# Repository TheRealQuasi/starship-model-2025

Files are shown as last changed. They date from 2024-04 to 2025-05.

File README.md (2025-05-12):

# Starship model Project 2025

Modelling and control of an electric reusable rocket
----------------------------------------------------

This project is part of a bachelor theisis at Chalmers University of Technology, department of electrical engineering ([Full report](/Bachelor_thesis_EENX16_24_50_Starship.pdf)
).

It is a continuation of a previous bachlor thesis from 2023, with the goal of buidling a propeller driven rocket model, immitating the control of SpaceX starships second stage.

The project involves programming a Teensy 4.1 microcontroller using PlatformIO in Visual Studio Code.

## Setup

1. Install Visual Studio Code.
2. Install the PlatformIO extension in Visual Studio Code.
3. Open the `Starship_25` folder in Visual Studio Code. PlatformIO should automatically detect all necessary files.

## Building and Programming

1. Connect the Teensy 4.1 microcontroller to your PC via USB.
2. Build the project by clicking on the checkmark icon in the bottom left corner of the PlatformIO interface.
3. Program the microcontroller by clicking on the arrow icon next to the checkmark.

## Dependencies

This project depends on the following libraries:

https://github.com/Seeed-Studio/Grove_6Axis_Accelerometer_And_Gyroscope_BMI088.git
https://github.com/budryerson/TFMini-Plus-I2C
https://github.com/bitcraze/Bitcraze_PMW3901

Please ensure these libraries are installed with platformIO before building the project. They should however be installed automatically when opening the project.

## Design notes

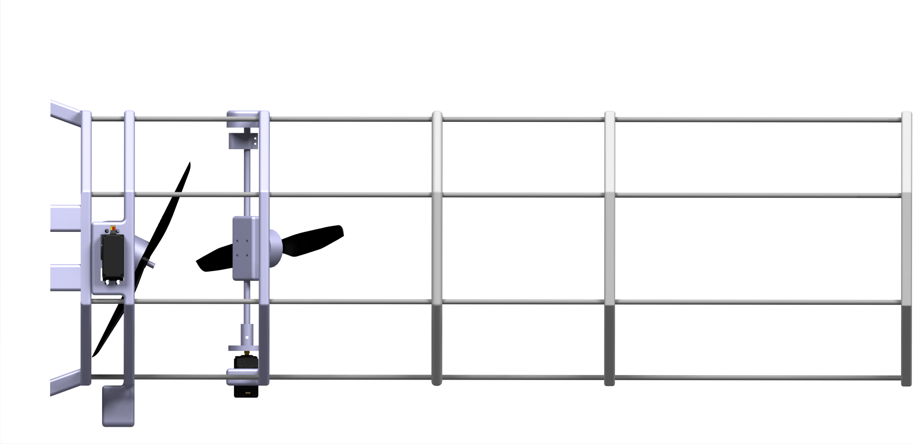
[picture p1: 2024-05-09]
CAD/Renders/Starship_render_sida1.png

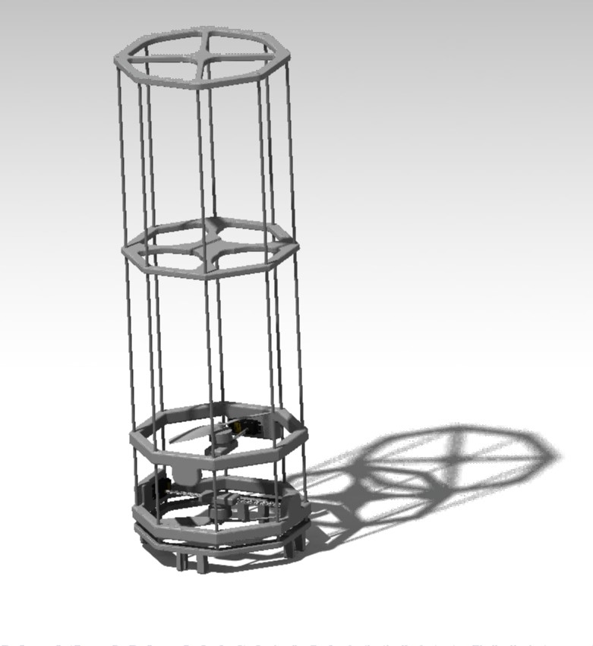
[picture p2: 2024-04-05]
CAD/Renders/Starship_render.jpg

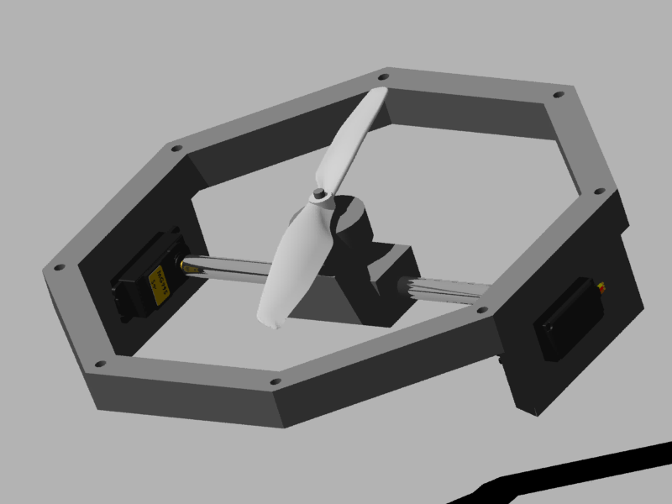
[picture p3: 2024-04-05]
CAD/Renders/Shooting 1.tif

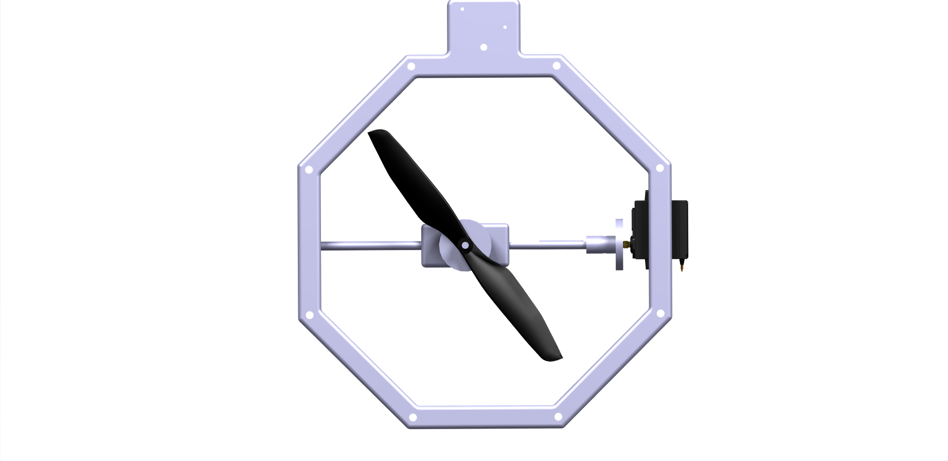
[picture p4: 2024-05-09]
CAD/Renders/Lidar_render.png

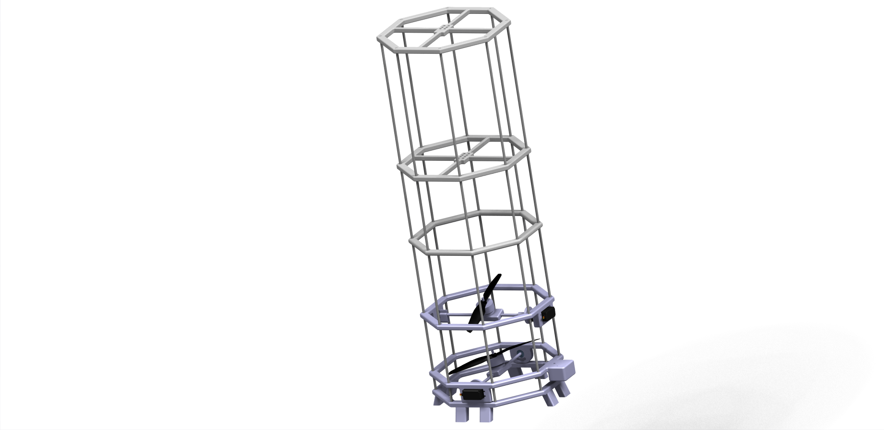
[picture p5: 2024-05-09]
CAD/Renders/Starship_render_startsida.png

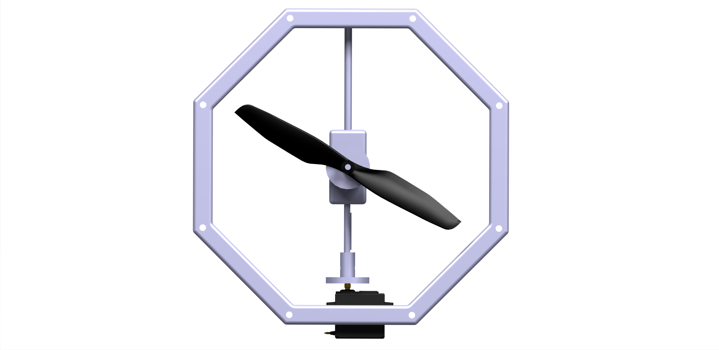
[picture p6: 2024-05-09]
CAD/Renders/Gimbal_render.png

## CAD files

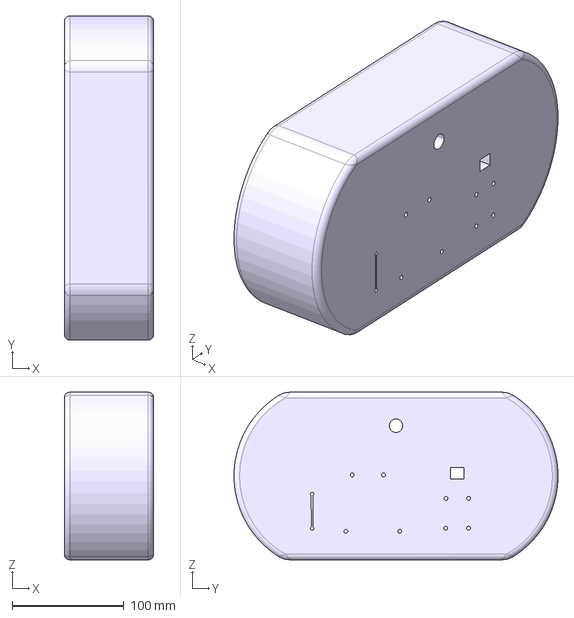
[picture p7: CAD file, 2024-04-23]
CAD/Prints/Handkontroll_Utskrift_1.stp
80.0 x 289.9 x 150.0 mm

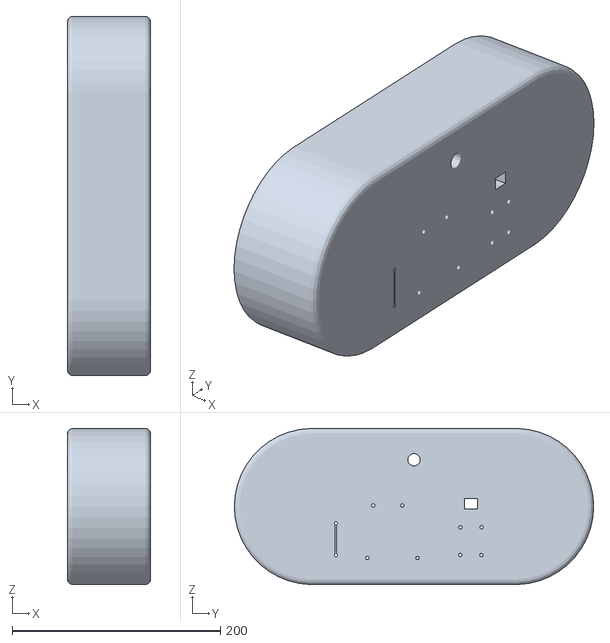
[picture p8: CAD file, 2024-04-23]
CAD/Prints/Handkontroll_utskrift_1.0.stl
80.0 x 345.5 x 150.0

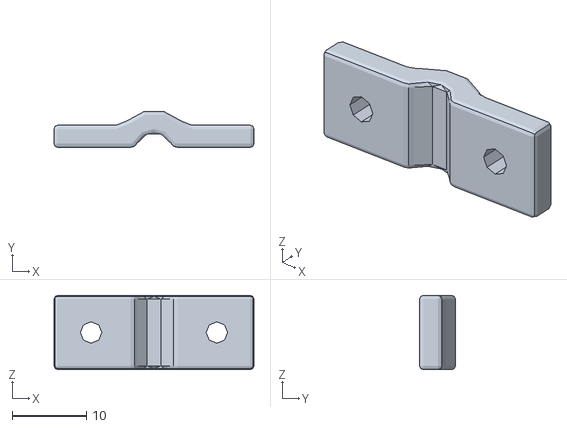
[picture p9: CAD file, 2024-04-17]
CAD/Prints/stav_klamma_utskrift.stl
27.0 x 4.83 x 10.0

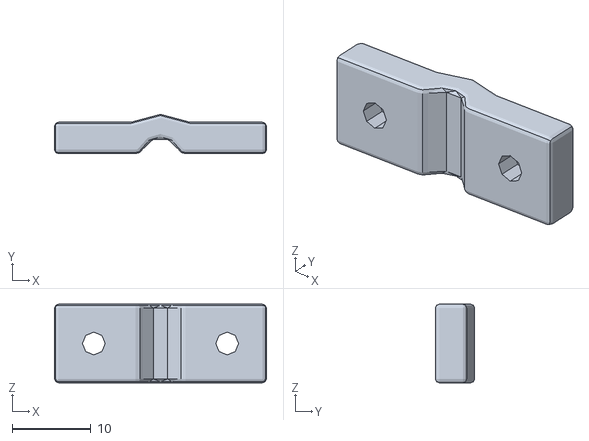
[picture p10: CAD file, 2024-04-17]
CAD/Prints/stav_mutterklamma_utskrift.stl
27.0 x 5.00 x 10.0

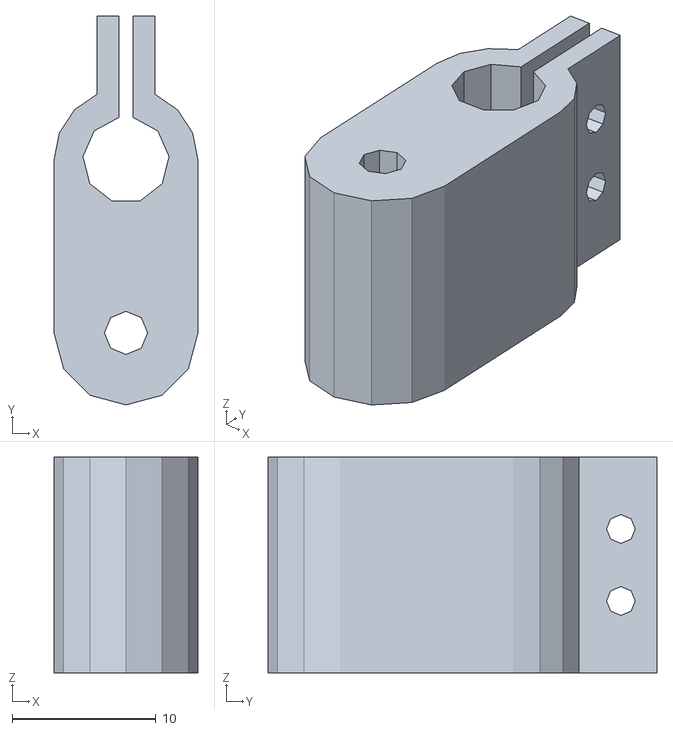
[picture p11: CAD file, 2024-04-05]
CAD/Prints/Klamma_stopp_utskrift_1.0.stl
10.0 x 27.0 x 15.0

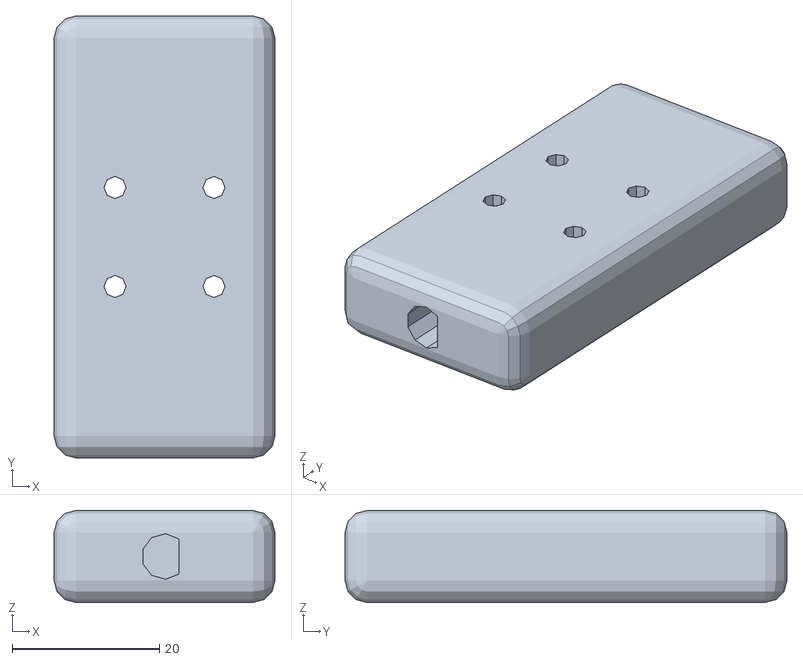
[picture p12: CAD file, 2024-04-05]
CAD/Prints/Blocktillmotorstang utskrift 1.1.stl
30.0 x 60.0 x 12.5

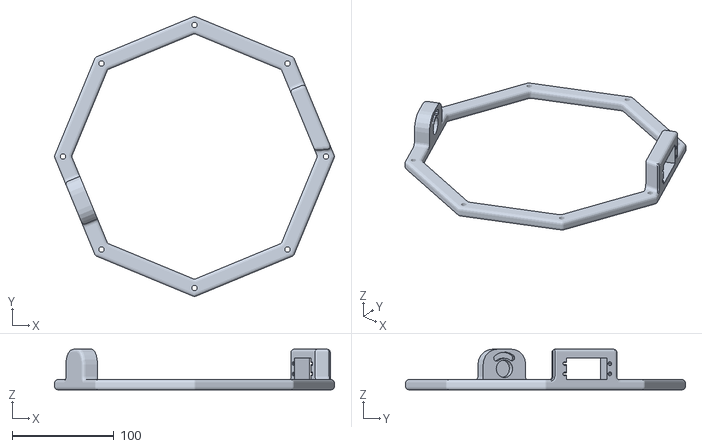
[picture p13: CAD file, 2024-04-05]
CAD/Prints/Hex_platta_utskrift_1.2.stl
275.5 x 275.5 x 40.0

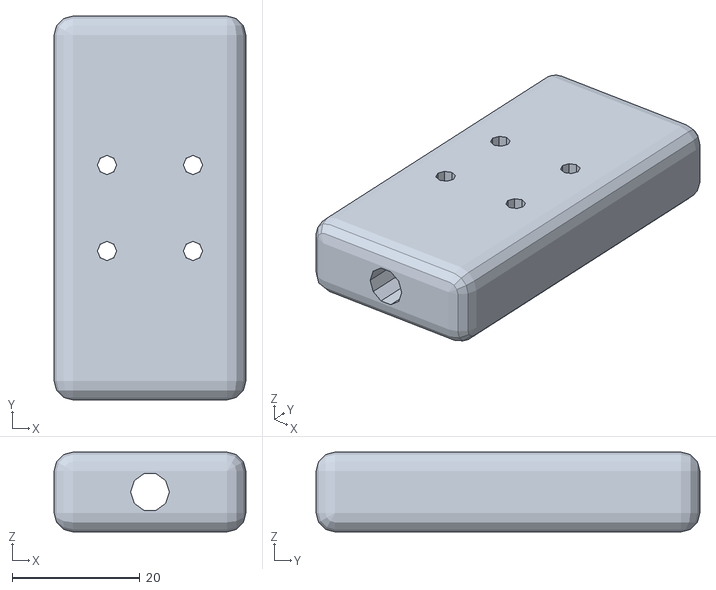
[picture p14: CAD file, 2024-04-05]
CAD/Prints/Blocktillmotorstang utskrift.stl
30.0 x 60.0 x 12.5

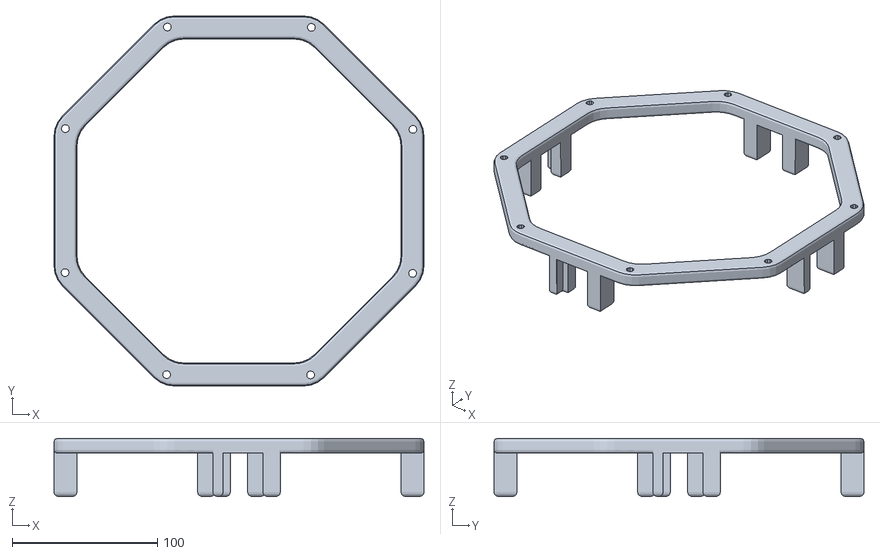
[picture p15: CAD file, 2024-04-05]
CAD/Prints/Bottenplatta_utskrift.stl
255.0 x 255.0 x 40.0

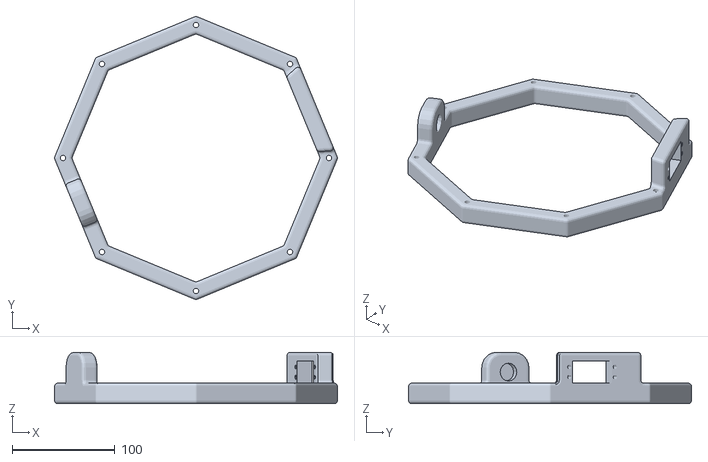
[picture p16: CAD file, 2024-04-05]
CAD/Prints/Hex_platta utskrift.stl
275.5 x 275.5 x 50.0

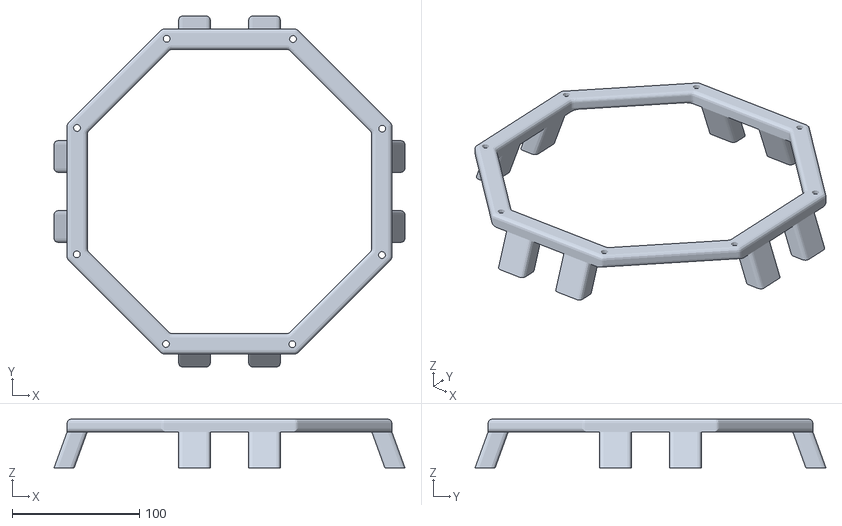
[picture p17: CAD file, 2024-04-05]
CAD/Prints/Bottenplatta_utskrift_1.stl
275.6 x 275.6 x 38.2

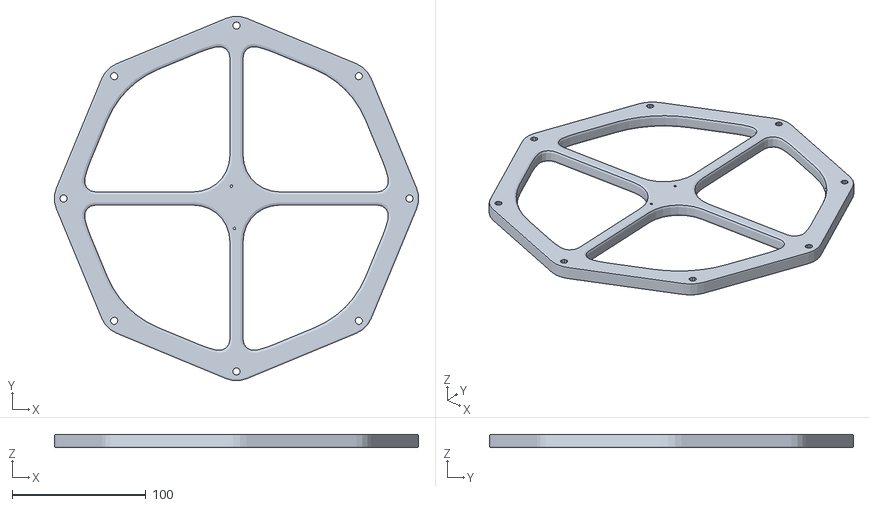
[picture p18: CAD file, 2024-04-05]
CAD/Prints/Toppplatta_utskrift.stl
272.4 x 272.4 x 10.0

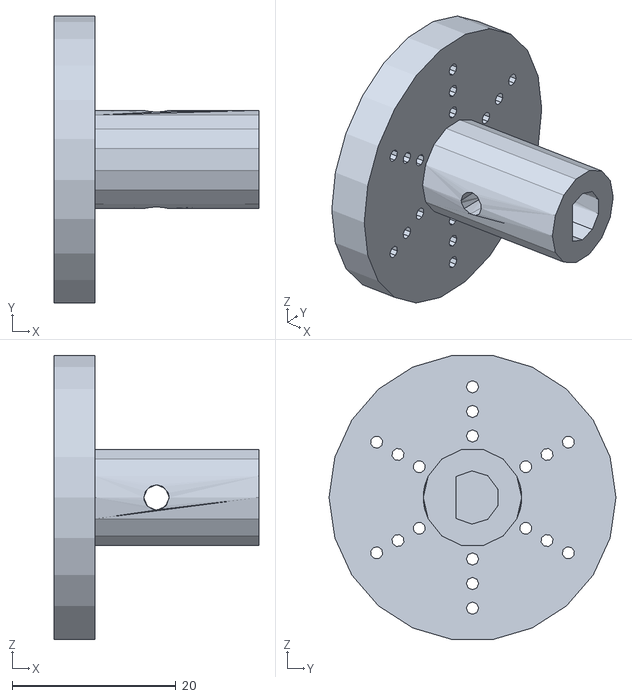
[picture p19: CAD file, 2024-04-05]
CAD/Prints/Klamma_stang_utskrift_1.1.stl
25.0 x 35.0 x 34.6

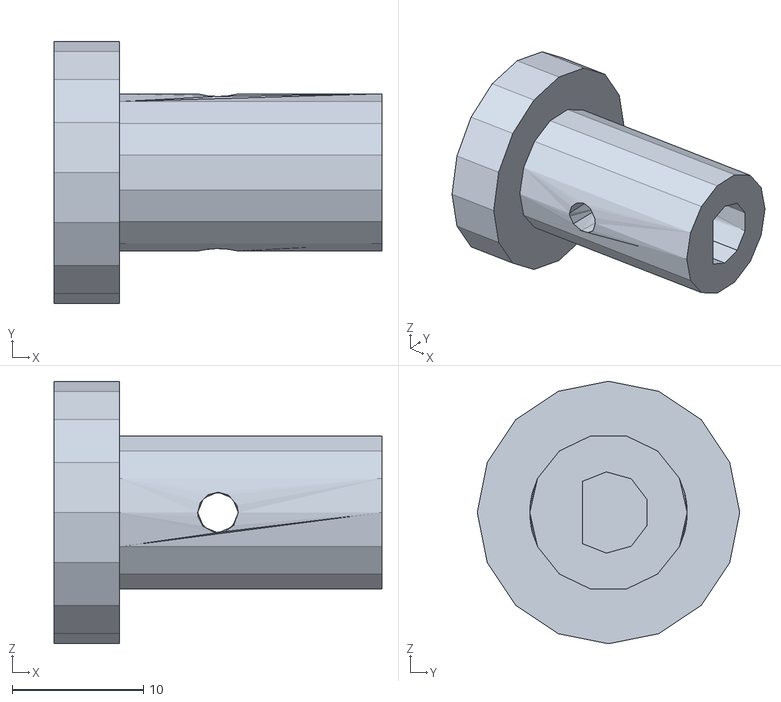
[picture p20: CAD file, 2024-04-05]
CAD/Prints/Klamma_stang_utskrift_1.0.stl
25.0 x 20.0 x 20.0

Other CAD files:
CAD/Prints/Hex_platta_utskrift_1.1.stl
CAD/Prints/Blocktillmotorstang_utskrift_1.2.stl
CAD/Prints/IMU_platta_utskrift_1.0.stl
CAD/Prints/TomPlatta_utskrift_1.0.stl
CAD/CAD_files/Blocktillmotorstang 1.0.CATPart
CAD/CAD_files/Blocktillmotorstang 1.1.CATPart
CAD/CAD_files/Bottenplatta.CATPart
CAD/CAD_files/Bottenplatta_1.1.CATPart
CAD/CAD_files/Handkontroll_1.0.CATPart
CAD/CAD_files/Handkontroll_1.1.CATPart
CAD/CAD_files/Hex_platta_1.0.CATPart
CAD/CAD_files/Hex_platta_1.1.CATPart
CAD/CAD_files/Hex_platta_1.2.CATPart
CAD/CAD_files/Hex_platta_1.3.CATPart
CAD/CAD_files/Hex_platta_1.4.CATPart
CAD/CAD_files/Klamma_stang_1.0.CATPart
CAD/CAD_files/Klamma_stang_1.1.CATPart
CAD/CAD_files/Klamma_stopp_1.0.CATPart
CAD/CAD_files/Kolfiberstang.CATPart
CAD/CAD_files/MG995.CATPart
CAD/CAD_files/Mittenplatta 1.0.CATPart
CAD/CAD_files/Mittenplatta 1.1.CATPart
CAD/CAD_files/Motorstang.CATPart
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

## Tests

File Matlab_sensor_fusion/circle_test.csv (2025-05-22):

timestamp | x1 | x2 | x3 | x4 | x5
2025-05-12T17:37:55.970376 | -0.01 | 0.02 | -6.77 | 3.05 | 0.01
2025-05-12T17:37:55.975332 | -0.01 | 0.02 | -6.77 | 3.05 | 0.01
2025-05-12T17:37:55.980794 | -0.01 | 0.02 | -6.77 | 3.05 | 0.02
2025-05-12T17:37:55.985734 | -0.01 | 0.02 | -6.77 | 3.05 | 0.01
2025-05-12T17:37:55.990682 | -0.01 | 0.02 | -6.77 | 3.05 | 0.01
2025-05-12T17:37:55.995787 | -0.01 | 0.02 | -6.77 | 3.05 | 0.01
2025-05-12T17:37:56.000909 | -0.01 | 0.02 | -6.77 | 3.05 | 0.01
2025-05-12T17:37:56.011162 | --0.01 | 0.02 | -6.77 | 3.05 | 0.01
2025-05-12T17:37:56.016248 | -0.01 | 0.02 | -6.77 | 3.05 | 0.02
2025-05-12T17:37:56.026483 | -0.0-0.01 | 0.02 | -6.77 | 3.05 | 0.01
2025-05-12T17:37:56.031572 | -0.01 | 0.02 | -6.77 | 3.05 | 0.02
2025-05-12T17:37:56.036802 | -0.01 | 0.02 | -6.77 | 3.05 | 0.02
2025-05-12T17:37:56.041821 | -0.01 | 0.02 | -6.77 | 3.05 | 0.01
2025-05-12T17:37:56.046927 | -0.01 | 0.02 | -6.77 | 3.05 | 0.01
2025-05-12T17:37:56.052062 | -0.01 | 0.02 | -6.77 | 3.05 | 0.02
2025-05-12T17:37:56.057142 | -0.01 | 0.02 | -6.77 | 3.05 | 0.01
2025-05-12T17:37:56.062260 | -0.01 | 0.02 | -6.77 | 3.05 | 0.01
2025-05-12T17:37:56.067464 | -0.01 | 0.02 | -6.77 | 3.05 | 0.02
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

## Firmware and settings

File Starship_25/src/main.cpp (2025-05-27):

#include <Arduino.h>
#include <Wire.h>
#include <SPI.h>
#include "Sensor_handler.h"
#include "Control.h"
#include "Killswitch.h"
#include "Motor_controller.h"
#include "Complementary_filter.h"
#include "Dead_reckoning_position.h"
#include "settings.h"
#include "Servo_controller.h"
#include <math.h>
#include "Madgwick6DOF.h"

//#define MADGWICK // Uncomment for Madgwick filter
#define COMPLEMENTARY // Uncomment for complementary filter
#define DEAD_RECKONING // Uncomment for dead reckoning

Madgwick6DOF filter; // Initialize the Madgwick filter with a beta value of 0.1

SensorHandler sensorHandler;
Control droneControl;

const float dt = 0.005f;
PositionEstimator estimator(dt);

void setup() {
    pinMode(9, INPUT);
    // Initialize serial communication to sensors
    Serial.begin(BAUDRATE);
    while (!Serial); // Wait for serial connection
    
    if (!sensorHandler.begin()) {
        Serial.println("Sensor initialization failed!");
        while (1);
    }
    Serial.println("All sensors initialized!");

    // Initialize kill switch
    setupKillSwitch(); // This is a non-blocking function that sets up the interrupt

    // Initialize drone control
    droneControl.initialize();
    //droneControl.testComponents();  // Test motors and servos
}

void printFixed(int value, bool end = false) {
    char buffer[7];  // 5 chars + null terminator
    snprintf(buffer, sizeof(buffer), "%5d", value);  // Right-aligned, 5 wide
    Serial.print(buffer);
    if (!end) {
        Serial.print(",");
    }
}

void loop() {

    if (emergencyStop) {
        // Stop motors
        motorsWrite(1,1050);
        motorsWrite(2,1050);
        while(emergencyStop){
            // Wait for the emergency stop to be released
            //Serial.println("Waiting for emergency stop to be released...");
            delay(100);
        };  // Infinite loop
        Serial.println("Resuming operation...");
    }

    SensorData data = sensorHandler.readSensors();

    #ifdef MADGWICK
        filter.update(data.imu_gyro_x, data.imu_gyro_y, data.imu_gyro_z,
                    data.imu_accel_x, data.imu_accel_y, data.imu_accel_z, dt);

        float yaw_m, pitch_m, roll_m;
        filter.getEulerAngles(yaw_m, pitch_m, roll_m);
        printFixed(yaw_m);
        printFixed(pitch_m);
        printFixed(roll_m);
    #endif

    #ifdef COMPLEMENTARY
        updateIMU(data.imu_accel_x, data.imu_accel_y, data.imu_accel_z,
                data.imu_gyro_x/131.072, data.imu_gyro_y/131.072, data.imu_gyro_z/131.072);
        // convert to degrees
        float yaw_deg = 2 * yaw * 180.0 / M_PI;
        float pitch_deg = 2 * pitch * 180.0 / M_PI;
        Serial.print(yaw);
        Serial.print(",");
        Serial.print(pitch);
        Serial.print(",");
    #endif

    // Update estimator
    #ifdef DEAD_RECKONING
        float flow_x, flow_y;
        flowToVelocityXY(data.flow_x, data.flow_y, data.lidar_dist/100.0, flow_x, flow_y);
        estimator.update({data.imu_accel_x, data.imu_accel_y, data.imu_accel_z},
                        pitch, yaw, data.lidar_dist/100.0, flow_x, flow_y);
        auto pos = estimator.getPosition();
        Serial.print(pos[0]);
        Serial.print(",");
        Serial.print(pos[1]);
        Serial.print(",");
        Serial.println(pos[2]); 
    #endif

    //float state[10] = {pos[0], vel[0], pos[1], vel[1], pos[2], vel[2],
    //                        pitch_m, yaw_m, data.imu_gyro_x, data.imu_gyro_y};
    //droneControl.lqrControl(state);

    if (manualControl) {
        droneControl.manualControl();
    } else {
        droneControl.autoControl(pitch_deg, yaw_deg);
    }
}

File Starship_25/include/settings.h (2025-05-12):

#ifndef SETTINGS_H
#define SETTINGS_H
// ==============================
// Global settings for the rocket
// ==============================

/*
* This file contains all the global settings and neasessery parameters
* It is a common place that makes adjustments easier
* 
* By GunnarEdman (Gunnar Edman),
* Emlzdev (Emil Reinfeldt)
*/

// Enable / disable settings
// =================================================================
// Change debug mode | COMMENT OUT WHEN NO COMPUTER CONNECTED
// #define DEBUG
#define DISABLE_COM
#define TIME_LIMIT 8000
#define LOOP_RATE
// #define ROLLCONTROLLER
#define MOTORS_SERVOS

// =================================================================


// Reference values
#define ALT_REF 1


// =============================================================================================
//  Pin assignments 
// ===============z==============================================================================

// ====== Motor and servo pin assignment ======
#define MOTOR_1_PIN 7  //4  // Lower motor
#define MOTOR_2_PIN 8  //5  // Upper motor
#define SERVO_1_PIN 2       // Lower servo (xRot = imu.roll_IMU)
#define SERVO_2_PIN 3       // Upper servo (yRot = imu.pitch_IMU)
#define CAL_BUTTON  37 //6
#define RED_LED_PIN 41 

#define SERVO_1_CONTROL_PIN 26
#define SERVO_2_CONTROL_PIN 27
#define THTOTLE_COTROL_PIN 1
// // ===== Radio pin assignment =====
// Define the pins used for the nRF24L01 transceiver module (CE, CSN)
//#define CE_PIN 9    //9 teensy, 2 arduino uno (lighter color)
//#define CSN_PIN 10  //10 teensy, 4 arduino uno (lighter color)



// // =============================================================================================
// //  Constants 
// // =============================================================================================

// ===== Killswitch settings =====
#define KILL_SWITCH_PIN 0  // Pin connected to kill switch channel
#define KILL_SWITCH_START_THRESHOLD 10 // Times to wait before kill switch is activated 

// ===== Div settings =====
#define BLINK_COUNT 5

// ====== Motor and servo constants ======
// #define SPEED_PROCENT_LIMIT 100
#define SPEED_LIMIT 1700                // Maximum allowed motor speed [us]
#define SPEED_MIN 1100                  // Lowest allowed motor speed
#define SERVO_1_HOME 55 //82;          // 0 position [degrees]
#define SERVO_2_HOME 71 //107; // 88;  // 0 position[degrees]
#define MAX_GIMBAL 30

// ====== Ground control specs ======
#define CAL_BUTTON_DURATION 2000        // How long the botton needs to hold to enter esc calibration [ms]

// ====== I2C interface ======
#define I2C_CLOCKSPEED 400000
#define IMU_ADR 0x68 //b1101000 // Sensor adress for I2C communication
//#define PRESSURE_SENSOR_ADR 0x77 // Default adress and does not need to be given

// ====== Radio Configuration ======
// Define transmit power level | RF24_PA_MIN, RF24_PA_LOW, RF24_PA_HIGH, RF24_PA_MAX
//#define RF24_PA_LEVEL RF24_PA_LOW
// Define speed of transmission | RF24_250KBPS, RF24_1MBPS, RF24_2MBPS
//#define RF24_SPEED RF24_2MBPS
// What radio channel to use (0-127). The same on all nodes must match exactly.
//#define RF24_CHANNEL 124

// #define TX_INTERVAL_MILLIS 

// ====== Other ======
// Baudrate for serial communication to terminal on computer
#define BAUDRATE 921600//6000000 //500000//6000000

/* // Timeout to wait before skipping a task
#define TIMEOUT_DURATION 15000000 // 15 seconds */

// ======== Roll Configuration =================================
#define ROLL_Kp 3     // Proportional gain



// =============================================================================================
//  Sensor configuration
// =============================================================================================
// ====== IMU Configuration ======
// BMI088 settings

// Filter parameters - Defaults tuned for 2kHz loop rate; Do not touch unless you know what you are doing:

// Default
// -----------------------------
// #define MADGWICK_FREQUENCY 2000          // Main loop frequency (the same as mdagwick filter frequency)
// #define CONTROLLER_FREQUENCY 100         // The frequency at which the LQR recalculates the control values
// #define CALIBRATION_COUNT 10000 //20000;
// #define WARMUP_TIME 100//21000 //10000

// #define B_MADGWCIK 0.04 //0.02; //0.04;    // Madgwick filter parameter (tuned for MPU MPU6050 or MPU9250)
// #define B_ACCEL 0.25//0.25//0.14                       // Accelerometer LP filter paramter, (MPU6050 default: 0.14. MPU9250 default: 0.2)
// #define B_GYRO 0.25//0.25//0.1                         // Gyro LP filter paramter, (MPU6050 default: 0.1. MPU9250 default: 0.17)

// #define ACC_RANGE_SETTING RANGE_6G
// #define ACC_RATE_SETTING ODR_1600

// #define GYRO_RANGE_SETTING RANGE_2000
// #define GYRO_RATE_SETTING ODR_2000_BW_532
// -----------------------------
// Default
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

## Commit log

2024-02-14 Initial creation of files to microcontroller and I2C protocol
2024-02-16 Added setup for sensors and started on retriving data sfom sensors
2024-03-07 Fixed Dps to send data
    [main.cpp]
2024-03-08 Restructured main.cpp and added debug variable, uncommented IMU code
2024-03-11 Made delay as non-blocking for reading data, added template for IMU
2024-03-11 Removed old test code for IMU
2024-03-15 Created code for transmission on reciverside, ground controller
2024-03-15 Removed old lib from IMU test
2024-03-15 Commented out I2Cdev.h
2024-03-22 Fixes on rocket and controller
    [main.cpp]
2024-03-28 Fixed controller inputs and improvements overall
    [main.cpp]
2024-03-28 Prepped for arduino use
2024-03-28 Added test projects for wireless communication
2024-04-05 Moved files to folders
    [Blocktillmotorstang 1.0.CATPart, Blocktillmotorstang 1.1.CATPart, Blocktillmotorstang utskrift 1.1.stl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]
2024-04-05 Added test folder and moved wireless comm
2024-04-09 Motor and servo control added
    Added the servo and motor control to the main rocket plaftorm IO project.
2024-04-09 Added the calButton to the ground control
    In the struct (ControlData), a byte "calButton" was added in the rocket program. The corresponding byte needs to be present in the ground controller aswell, since it sends / reads the same data strea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
2024-04-10 Fixed bug with teensy crashing and added a handshake
    [main.cpp]
2024-04-10 Moved config to settings and fixed bug with calButton
    [main.cpp, settings.h]
2024-04-10 IMU, madgwick-filtering and lidar added
    This commit contains the addition of a class Imu6DOF that contains all functionalities and variables for getting imu-data and filtering it with a madgwick filter.
    Also added lidar-functionalities in main.cpp.
2024-04-10 Merged main into IIMUs_and_lidar
    Fixed conflicts in order to prepare for merging with main.
    [settings.h]
2024-04-11 Corrected main.cpp after wrong merge
    [main.cpp]
2024-04-21 Restructure of servo, ESC, IMU and phase message transmission flags
    Tweaked the structure of code in the named areas. Also added flags / to do where phase messages should be sent to notify the pilot of the different phases during setup.
2024-04-23 Added update to ground control side
2024-04-23 Fixed a typo from the merge of phase message transimssions
    [main.cpp]
2024-04-28 LQR control implemented + generel fixes
    LQR implemented ahead of starship test flight 2.
    This branch also contains the latest features from the PID_control_V1-branch, including telemetry logging to the onboard SD-card
    [main.cpp, settings.h]
2024-04-29 Fixed the states / variables contained in the senderData struct
    [main.cpp, settings.h]
2024-04-29 Fixed time management (LQR frequency regulation)
    [main.cpp, settings.h]
2024-04-29 A bunch of bug fixes
    [main.cpp, settings.h]
2024-04-29 More CSV to SD-card fixes
    [main.cpp, settings.h]
2024-05-02 More changes to LQR and debug prints
2024-05-03 More changes in imu.h
2024-05-03 Added roll regulation, changed motorWrite to take motorNum
2024-05-04 IMu sampling tweaks + RPM mapping added
2024-05-06 Added lidar calibration (offset from ground)
2024-05-06 More fixes with comments
    [main.cpp]
2024-05-07 Commented out a bug in the end of setup()
    [main.cpp, settings.h]
2024-05-08 Trying to run the I2C bus at 400 kHz (not working for the lidar)
    [main.cpp, settings.h]
2024-05-08 Changed to 400kbps i2c and fixed lidar to give data
    [main.cpp, settings.h]
2024-05-10 Madgwick filter fixed + other bug fixes
    The code used when flying 2024-05-09
    [main.cpp, settings.h]
2024-05-26 Fixed roll-control + final tests version
    This is the version of the code used during the exhibition in "studiehallen". Almost identical to what was used during the fnal tests seen in the final report (apart from these bug fixes in roll-control).
    [main.cpp, settings.h]
2025-03-06 Start of branch electrnocs with imu_test
2025-03-06 Sensor Handler
2025-03-07 Trying to implement IMU, currently wrong!
    [main.cpp]
2025-03-11 Tried to add LiDar files
2025-03-11 Small changes Lidar (Not solved yet)
2025-03-11 Added temp in IMU and PIN_WIRE1_SDA 18, PIN_WIRE1_SCL 19 in TFMPI2C
2025-03-12 Tried to add Optical flow with Bitcraze_PMW3901 library. Not tested
2025-03-12 Wire1 on pins 16 and 17
2025-03-13 Lidar and IMU sensors integrated
2025-03-21 Motor and Servo files
2025-03-24 Sensor code activated
2025-03-31 Kill Switch implemented
    Can't have while-loop in irq to not break system so either system reset instead or global flag
    [main.cpp]
2025-04-01 Working kill switch that restarts teensy4.1
2025-04-10 Added irq handler for optical flow sensor
2025-04-11 Work on sensor fusion
2025-04-11 Sensor fusion matlab plots to help visualize IMU readings
    [imu_data_extracted.csv]
2025-04-16 Changed interupt pin to pin 9 an pin to input_pullup. renamed flow to flow_PWM3901 to not confuse with Sensor_handler flow varaible
2025-04-16 Changed LiDar frame rate to 1000 and removed delay in get data function
2025-04-16 Changed killswitch to allow for arm and disarm, removing system reset. Moved defines to settings.h and added threshold setting
    [settings.h]
2025-04-22 Extended Kalman Filter test
    [structured_sensor_data.csv]
2025-04-24 Added manual control of servos and motors as well as manual and automatic mode
2025-05-07 Matlab fixes
    [all_sensor_shake_data.csv]
2025-05-08 Simulation tested
    [all_sensor_shake_data.csv, data2_log_all.csv]
2025-05-22 LQR test implem + Madgwick + Kalman tests
    [Madgwick_output.csv, circle_test.csv]
